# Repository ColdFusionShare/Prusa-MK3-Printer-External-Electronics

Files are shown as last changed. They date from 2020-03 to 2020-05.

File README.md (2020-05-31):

# Prusa External Electronics
A project to enable moving PSU, EINSY, and LCD out of your enclosure.

- BOM (updated with missing front and back panel parts)
- Fusion 360 source files added

Overall View:
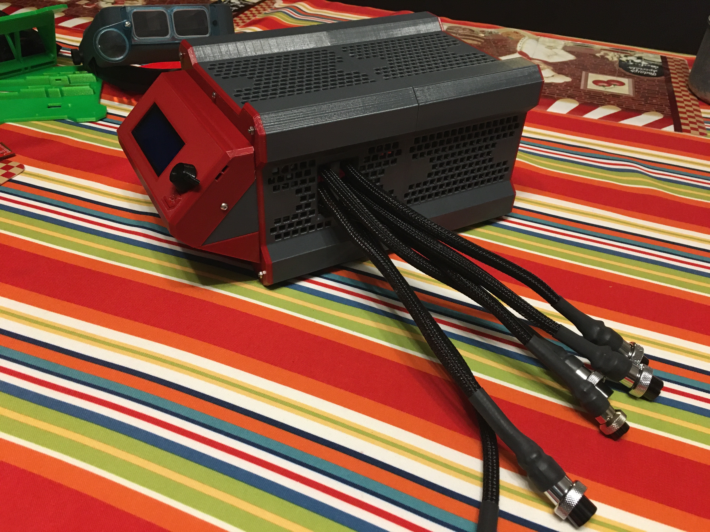
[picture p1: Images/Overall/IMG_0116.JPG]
Overall View


Cable Gland:
- Detaches easily to allow EINSY to slide back without taking cabling apart.
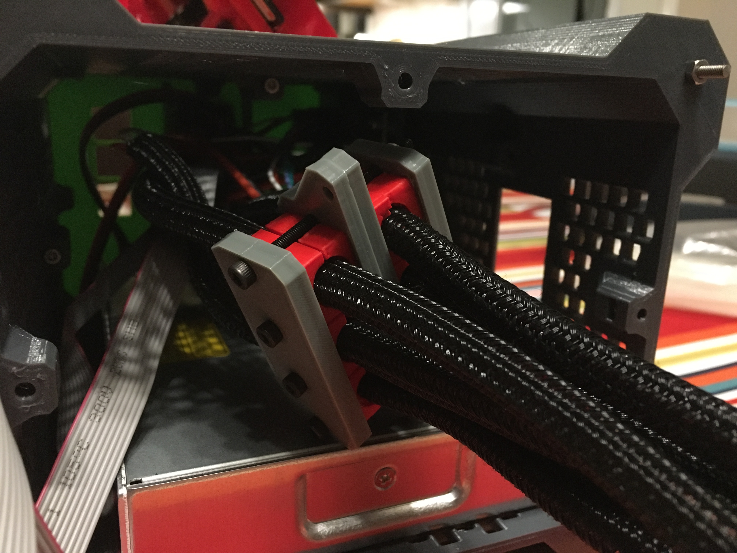
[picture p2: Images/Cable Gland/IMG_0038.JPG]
Cable Gland


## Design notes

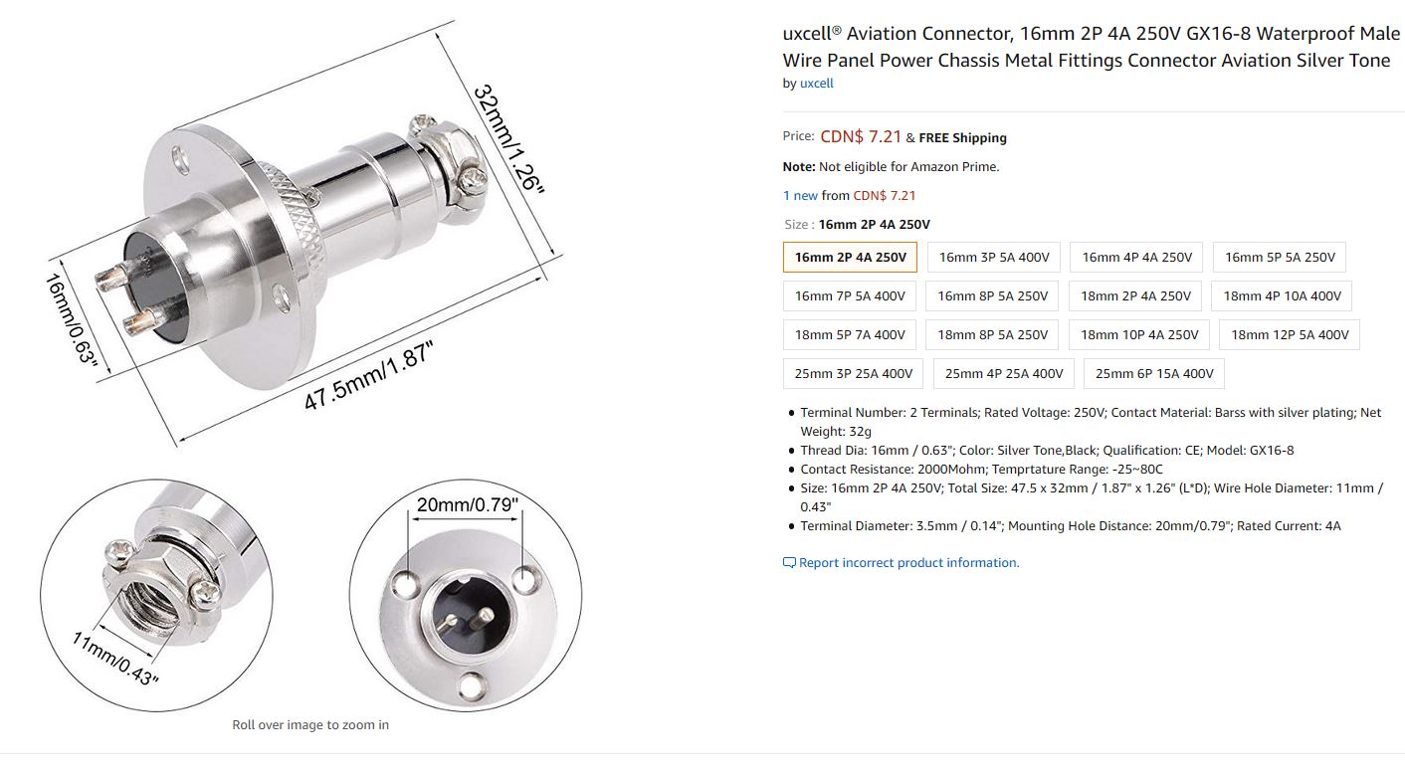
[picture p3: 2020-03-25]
Docs/gx20_16mm.JPG

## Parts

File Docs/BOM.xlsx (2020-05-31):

Item | Description | Assembly | Quantity Required | Sourced From | Part No | Lead-Time | Link | Comment
1 | 18mm 10P 4A 250V | External case cables & Lower Printer Case | 1 | Ebay |  | long | https://www.ebay.com/itm/WD19-GX20-2pin-12Pin-Aviation-Plug-Connector-19mm-20mm-Mount-Circular-Bulkhead/132708407252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
 |  |  |  |  |  |  | (link is for all circular connectors - make sure to pick the correct ones from the list and not the link above)
2 | 18mm 8P 5A 250V | External case cables & Lower Printer Case | 1 | Ebay |  | long
3 | 18mm 12P 5A 400V | External case cables & Lower Printer Case | 1 | Ebay |  | long
4 | 16mm 9P 4A 250V | External case cables & Lower Printer Case | 1 | Ebay |  | long
5 | 18mm 4P 10A 400V | External case cables & Lower Printer Case | 1 | Ebay |  | long
6 | 16mm 6P 7A 400V | External case cables & Lower Printer Case | 1 | Ebay |  | long
7 | Black socket connector - 5 pin |  | 1 | Digikey | WM2536-ND | Short |  | Single connector Y for MMU2 and PINDA2
8 | Black socket connector - 4 pin |  | 5 | Digikey | WM2535-ND | Short
9 | Black socket connector - 3 pin |  | 2 | Digikey | WM2534-ND | Short
10 | Black socket connector - 2 pin |  | 2 | Digikey | WM2533-ND | Short
11 | Contacts for Housing housings above |  | 50 | Digikey | WM2515-ND | Short
12 | Black connector - 5 pin |  | 1 | Digikey | WM8037-ND | Short |  | Single connector for MMU2 and PINDA2 connections
13 | Contacts for black connector above |  | 10 | Digikey | WM2580CT-ND | Short
14 | Black connector - 4 pin |  | 5 | Digikey | WM2902-ND | Short
15 | Black connector - 3 pin |  | 2 | Digikey | WM2901-ND | Short
16 | Black connector - pin |  | 2 | Digikey | WM2900-ND | Short
17 | Contacts for Housing housings above |  | 50 | Digikey | WM2512-ND | Short
18 | Self wrap 1/4" x 25' black |  | 1 | Digikey | 1030-FN0.25BK25-ND | Short
19 | Heat shrink 3:1 with glue 1/2" |  |  | Digikey |  | Short |  | I did not get glue and they came loose
20 | Heat shrink for circular connectors
 | depends on wire size - just get a selection |  |  | Digikey |  | Short
 | to use
21 | M3 bolts and nuts - various lengths | General
22 | M3 bolts long for cable gland (measure) | General
23 | M3 threaded rods 250 mm length | General | 4 | Amazon |  | Medium
25 | PWR ENT MOD RCPT IEC320-C14 PNL | External Case Back Cover | 1 | Digikey | Q307-ND | Short
 | 10A
26 | FUSE GLASS 5A 250VAC 5X20MM | External Case Back Cover | 2 | Digikey | F1748-ND | Short
 | (or similar 5A of this size) |  | Get spares
24 | SWITCH PUSHBUTTON SPST 5A 125V | External Case Front Cover | 1 | Digikey |  | Short
26 | 24 VDC Fan - looking for specs | External Case Front Cover | 1 | Digikey | ? | Short

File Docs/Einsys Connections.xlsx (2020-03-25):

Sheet: Pin Reference
 |  | 31 pins
 |  |  |  |  |  |  |  |  | Cable Connector | Plug In Connector
 |  |  | EINSY |  |  |  |  |  | Vendor | Vendor
Cable | Function | Name | Board Connector | Pin | Pin Detail | Wire Size | Pin Count | Vendor | Part No | Part No | Voltage | Current
Motors
 | Stepper Motor | Motor X | J8 | 1 |  | 22-24 | 4 | Digikey | WM2902-ND | WM2535-ND
 |  |  |  | 2 |  | 22-24
 |  |  |  | 3 |  | 22-24
 |  |  |  | 4 |  | 22-24
 | Stepper Motor | Motor Y | J9 | 1 |  | 22-24 | 4 | Digikey | WM2902-ND | WM2535-ND
 |  |  |  | 2 |  | 22-24
 |  |  |  | 3 |  | 22-24
 |  |  |  | 4 |  | 22-24
 | Stepper Motor | Motor Z1 | J10 | 1 |  | 22-24 | 4 | Digikey | WM2902-ND | WM2535-ND
 |  |  |  | 2 |  | 22-24
 |  |  |  | 3 |  | 22-24
 |  |  |  | 4 |  | 22-24
 | Stepper Motor | Motor Z2 | J11 | 1 | shared with Z1 | 22-24 |  | Digikey | WM2902-ND | WM2535-ND
 |  |  |  | 2 | shared with Z1 | 22-24
 |  |  |  | 3 | shared with Z1 | 22-24
 |  |  |  | 4 | shared with Z1 | 22-24
 |  |  |  |  | Total |  | 12
Extruder Cable
 | Stepper Motor | Extruder | J12 | 1 |  | 22-24 | 4 | Digikey | WM2902-ND | WM2535-ND
 |  |  |  | 2 |  | 22-24
 |  |  |  | 3 |  | 22-24
 |  |  |  | 4 |  | 22-24
 |  |  |  |  |  |  |  |  |  |  |  | All Steppers | 16
 | Fan | Hot End Fan | J5 | 1 |  | 24 | 3 | Digikey | WM2901-ND | WM2534-ND
 | 5V |  |  | 2 |  | 24
 |  |  |  | 3
 | Fan | Print Fan | J4 | 1 |  | 24 | 3 | Digikey | WM2901-ND | WM2534-ND
 | 5V |  |  | 2 |  | 24
 |  |  |  | 3 |  | 24
 | Extruder | Thermistor | J2 | 1 | GND | 24 | 2 | Digikey | WM2900-ND | WM2533-ND
 |  |  |  | 2 |  | 24
 | Extuder Heater | Heater | X13 | 1 |  | 20? | 2 | Digikey | 277-1011-ND | 277-1150-ND
 |  |  |  | 2 |  | 20?
 | Pinda Sensor | Pinda Probe | J15 | 1 |  | 24 | 4 | Digikey | WM2902-ND | WM2535-ND
 |  |  |  | 2 |  | 24
 |  |  |  | 3 | GND | 24
 |  |  |  | 4 | VCC | 24
 | Filament Sensor | Filament Sensor | P3 (lower row) | 2 | VCC | 24 | 5 | Digikey | WM8037-ND | WM2536-ND
 |  |  | pins 2,4,6,8,10 | 4 | GND | 24
 |  |  |  | 6 |  | 24
 |  |  |  | 8 |  | 24
 |  |  |  | 10 |  | 24
 |  |  |  |  | Total |  | 23 |  |  |  |  | All Signal | 19
MMU
 | MMU connection |  | P3 (upper row) | 1 | VCC | 24 | 5 | Digikey | WM8037-ND | WM8249-ND
 |  |  | pins 1,3,5,7,9 | 3 |  | 24
 |  |  |  | 5 |  | 24
 |  |  |  | 7 | GND | 24
 |  |  |  | 9 |  | 24
 |  |  |  |  | Total |  | 5
Heat Bed
 | Heat Bed | Heat | Screw Terminal | 1 |  | 14 | 2
 |  |  |  | 2 |  | 14
 | Heat Bed | Thermistor | J6 | 1 | GND | 24 | 2 | Digikey | WM2900-ND | WM2533-ND
 |  |  |  | 2 |  | 24
 |  |  |  |  | Total |  | 4 |  |  |  |  | All Heater Lines | 4
 |  |  |  |  | Grand Total |  | 44
 |  |  |  |  |  |  |  |  |  |  |  | Total | 39
 | Power Failure | Power Panic |  | 1 |  |  | 2 | Digikey | WM2900-ND
 |  |  |  | 2
 | Bed Power Input | PSU Power IN |  | 1 |  |  | 2
 |  |  |  | 2
 | Power Input | PSU Power IN |  | 1 |  |  | 2
 |  |  |  | 2
 | https://github.com/PrusaOwners/prusaowners/wiki/MK3_Compatible_Parts
 | erminal / Pin for keyed connectors | Female terminals (pins) used in 4-pin and 3-pin keyed connectors on the Einsy board. |  | Molex: 16-02-0097 | Mouser: 538-16-02-0097 (https://www.mouser.com/ProductDetail/Molex/16-02-0097?qs=sGAEpiMZZMtVoztFdqDXO%252bpSlI4T0Hse)
 |  |  |  |  | DigiKey: WM2513-ND (https://www.digikey.com/products/en?keywords=16-02-0097)
 |  |  |  |  | TME: MX-16-02-0097 (https://www.tme.eu/en/details/mx-16-02-0097/raster-signal-connectors-254mm/molex/016020097-70058-0206/)

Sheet: Wiring Guide
 | External Case | EINSY |  |  |  |  |  |  |  | Printer Side
 | Circular Connector Type | Connector | Prusa | My |  |  | Board | Board |  | In-line connector
Signal Type | (for cables going outof case) | Pin Number | Color | Color | Function | Name | Connector | Pin |  | (from bulk head circular Connectors) | AWG | Comment
Motor
 | 18mm 10P 4A 250V
 |  | 1 | Black | Black | Stepper Motor | Motor X | J8 | 1 |  | WM2535-ND | 22
 |  | 2 | Green | Green |  |  |  | 2
 |  | 3 | Red | Red |  |  |  | 3
 |  | 4 | Blue | Blue |  |  |  | 4
 |  | 5 | Black | Black | Stepper Motor | Motor Y | J9 | 1 |  | WM2535-ND | 22
 |  | 6 | Green | Green |  |  |  | 2
 |  | 7 | Red | Red |  |  |  | 3
 |  | 8 | Blue | Blue |  |  |  | 4
 |  | 9 |  |  | Unused
 |  | 10 |  |  | Unused
 | 18mm 8P 5A 250V | 1 | Black | Black | Stepper Motor | Motor Z1/Z2 | J10/J11 | 1 |  | WM2535-ND | 22 | Split into two connectors for Z. For SKR 1.4 used 4 unused lines on 9 Pin circular connector
 |  | 2 | Green | Green |  |  |  | 2
 |  | 3 | Red | Red |  |  |  | 3
 |  | 4 | Blue | Blue |  |  |  | 4
 |  | 5 | Black | Black | Stepper Motor | Extruder | J12 | 1 |  | WM2535-ND | 22
 |  | 6 | Green | Green |  |  |  | 2
 |  | 7 | Red | Red |  |  |  | 3
 |  | 8 | Blue | Blue |  |  |  | 4
Signal
 | 18mm 12P 5A 400V
 |  | 1 | black | black | Fan | Hot End Fan | J5 | 1 |  | WM2534-ND | 22
 |  | 2 | red | red | 5V |  |  | 2
 |  | 3 | yellow | green | tach |  |  | 3
 |  | 4 | black | black | Fan | Print Fan | J4 | 1 |  | WM2534-ND | 22
 |  | 5 | red | red | 5V |  |  | 2
 |  | 6 | yellow | green | tach |  |  | 3
 |  | 7 |  | black | Extruder | Thermistor | J2 | 1 |  | WM2533-ND | 22
 |  | 8 |  | red |  |  |  | 2
 |  | 9 | white | white | Pinda Sensor | Pinda Probe | J15 | 1 |  | WM2535-ND
 |  | 10 | black | black |  |  |  | 2
 |  | 11 | blue | red |  |  |  | 3
 |  | 12 | brown | green |  |  |  | 4
 | 16mm 9P 4A 250V
 |  | 1 | white | white | Filament Sensor MK3S | Filament Sensor | P3 (lower row) | 2 |  | WM2536-ND
 |  |  |  |  |  |  | pins 2,4,6,8,10 | 4 | NC
 |  |  |  |  |  |  |  | 6 | NC
 |  | 2 | black | black |  |  |  | 8
 |  | 3 | red | red |  |  |  | 10
 |  | 4 |  | black | Heat Bed | Thermistor | J6 | 1 |  | WM2533-ND | 22
 |  | 5 |  | red |  |  |  | 2
 |  | 6 |  |  | Unused
 |  | 7 |  |  | Unused
 |  | 8 |  |  | Unused
 |  | 9 |  |  | Unused
Heat
 | 18mm 4P 10A 400V
 |  | 1 |  | Red | Extuder Heater | Heater | X13 | 1 |  | 16 AWG | 16 | Wago?
 |  | 2 |  | Black |  |  |  | 2
 |  | 3 |  | Red | Heat Bed | Heat | Screw Terminal | 1 |  | 14 AWG | 14 | Red screw terminals
 |  | 4 |  | Black |  |  |  | 2
MMU
 | 16mm 6P 7A 400V
 |  | 1 | brown | red | MMU connection |  | P3 (upper row) | 1 |  | WM2536-ND
 |  |  |  |  |  |  | pins 1,3,5,7,9 | 3 | NC
 |  | 2 | green | green |  |  |  | 5
 |  | 3 | white | white |  |  |  | 7
 |  | 4 | blue | blue |  |  |  | 9
 |  | 5 | red | red |  |  |  |  |  | mmu +24V | 16 | 16 AWG
 |  | 6 | black | black |  |  |  |  |  | mmu ground |  | 16 AWG

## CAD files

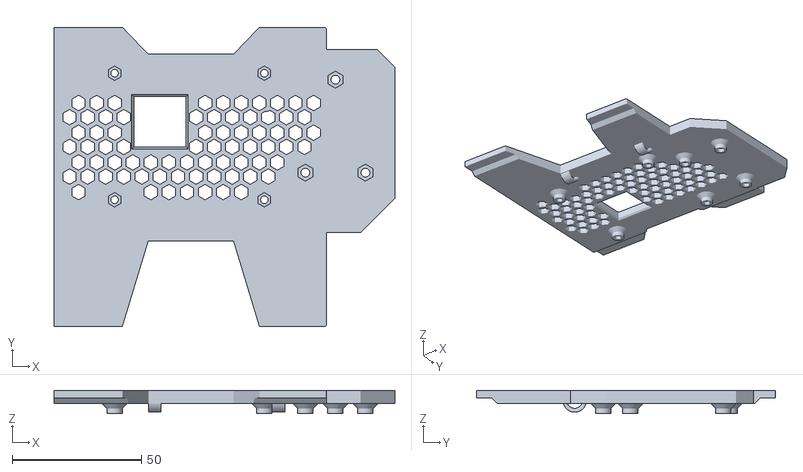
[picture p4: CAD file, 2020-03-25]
Printed Parts/Boards/PCB Holder (Rpi3).stl
132.0 x 115.7 x 9.00

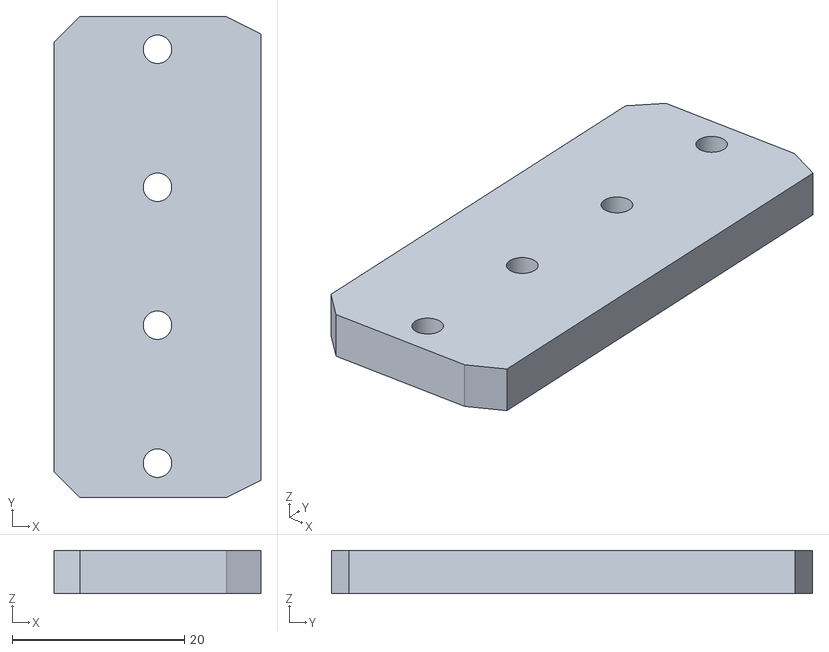
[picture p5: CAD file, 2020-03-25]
Printed Parts/Cable Gland/CGF Top.stl
24.0 x 55.8 x 5.00

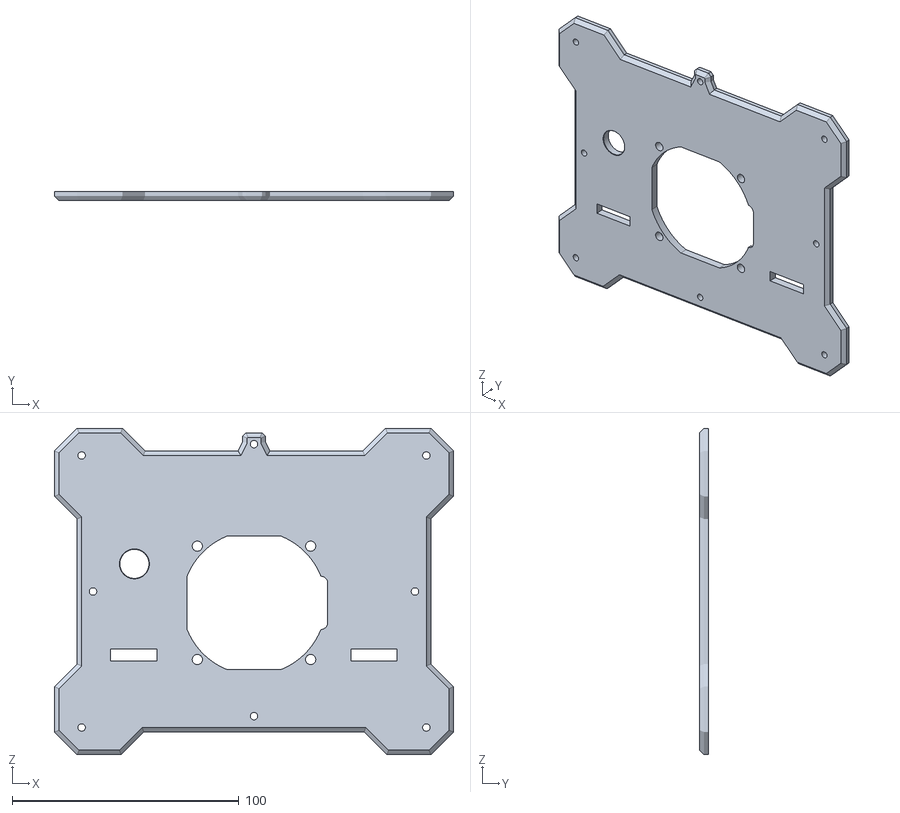
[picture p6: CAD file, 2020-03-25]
Printed Parts/Frame/FrameSlice_Front_Cover.stl
176.0 x 4.00 x 144.0

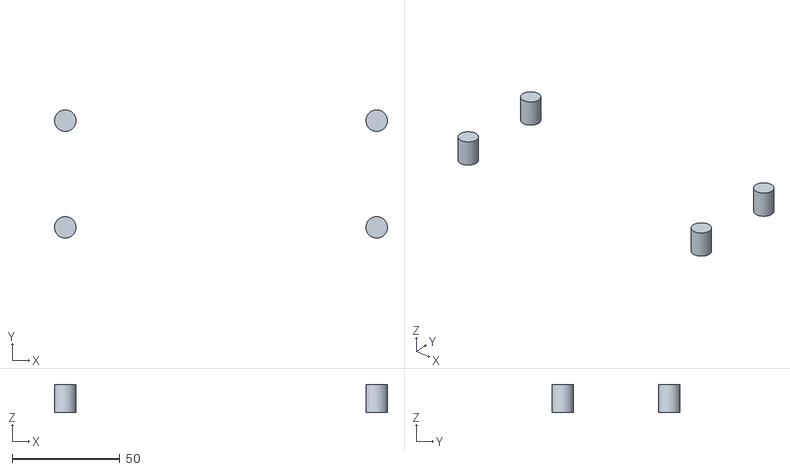
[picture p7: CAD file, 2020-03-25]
Printed Parts/LCD/LCD Custom Support Blockers.stl
154.5 x 59.5 x 13.1

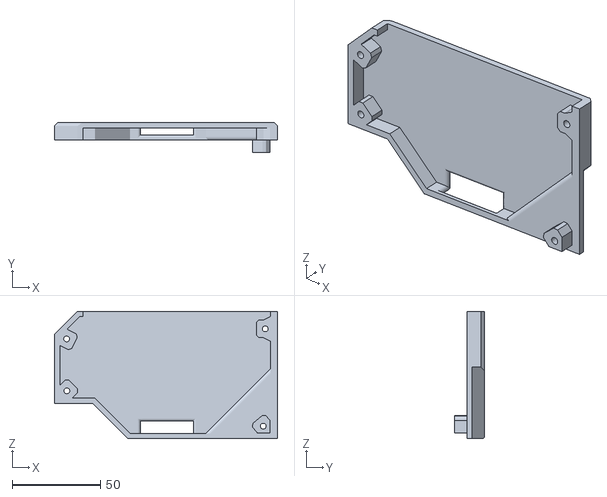
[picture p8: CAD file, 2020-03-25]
Printed Parts/Printer/Lower Case Cover v2.stl
126.0 x 17.0 x 72.0

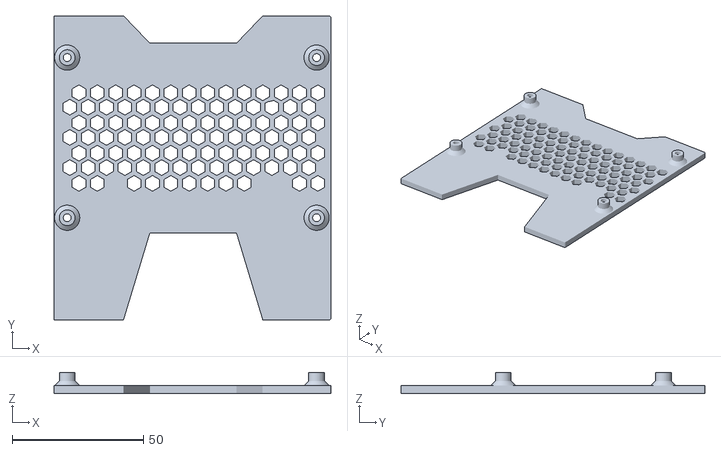
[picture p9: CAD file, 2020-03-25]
Printed Parts/Boards/PCB Holder (Einsy).stl
105.5 x 115.7 x 8.00

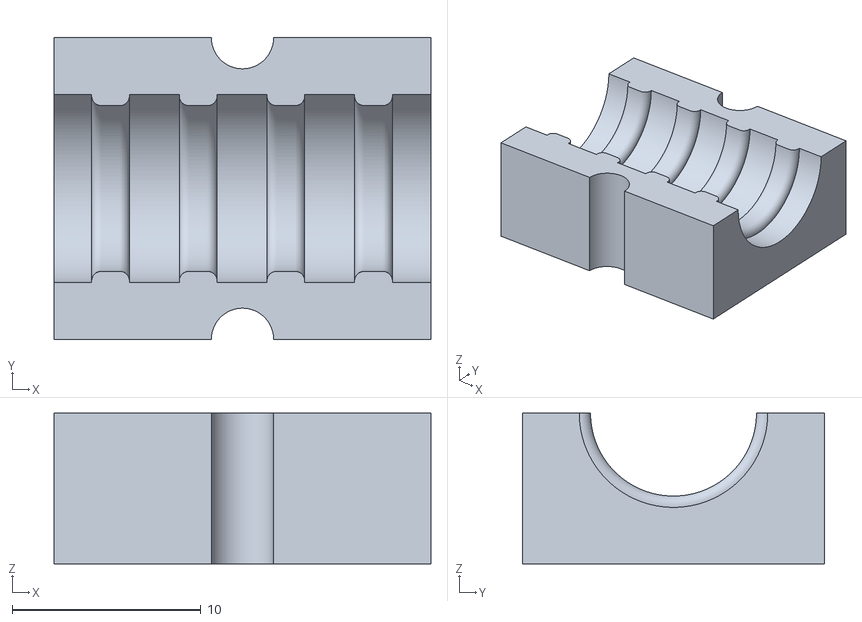
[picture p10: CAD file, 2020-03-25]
Printed Parts/Cable Gland/Cable_Gland_Bottom_Or_Top.stl
20.0 x 16.0 x 8.00

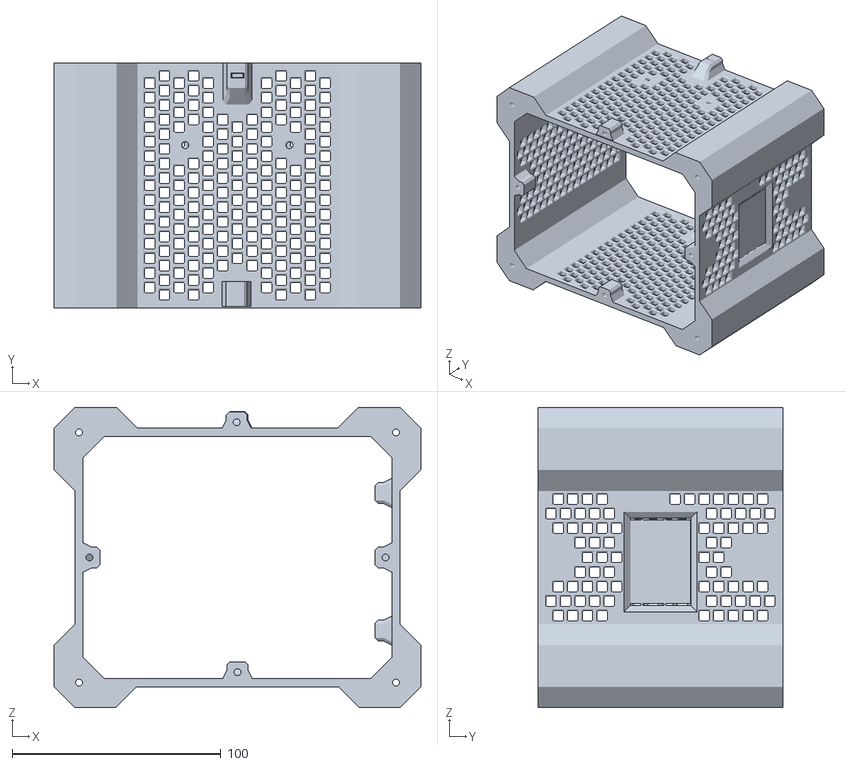
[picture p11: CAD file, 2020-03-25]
Printed Parts/Frame/FrameSlice_Front_v2.stl
176.0 x 117.5 x 144.0

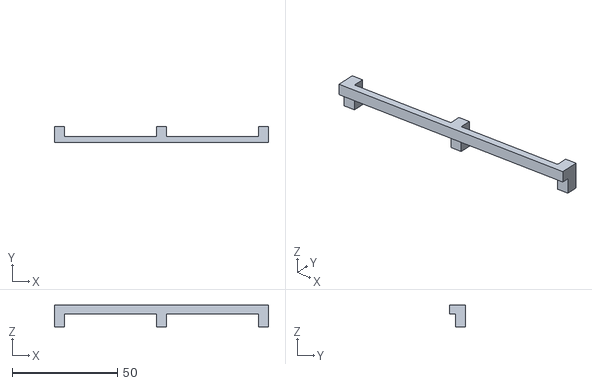
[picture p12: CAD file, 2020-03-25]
Printed Parts/LCD/LCD Lower Inside Support.stl
101.9 x 7.72 x 10.3

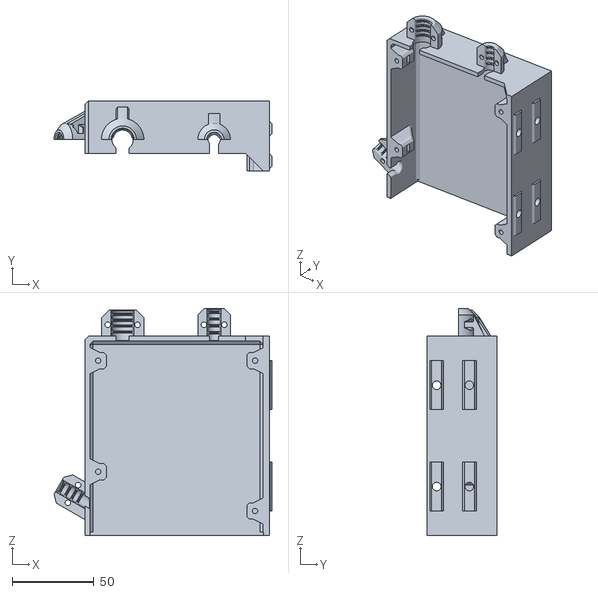
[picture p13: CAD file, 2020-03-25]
Printed Parts/Printer/Upper Case.stl
133.4 x 42.8 x 139.0

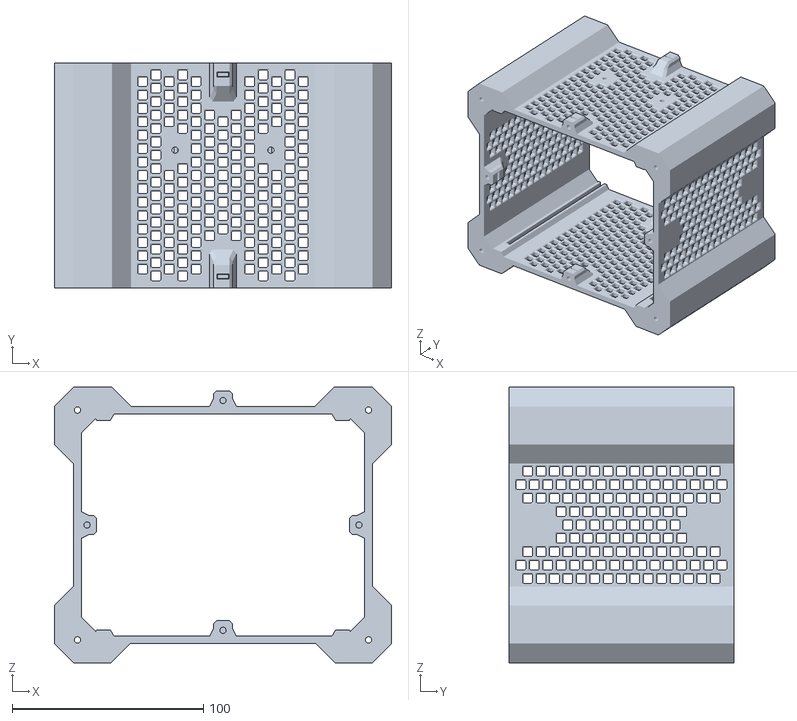
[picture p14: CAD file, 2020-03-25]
Printed Parts/Frame/FrameSlice_Back_v2.stl
176.0 x 117.5 x 144.0

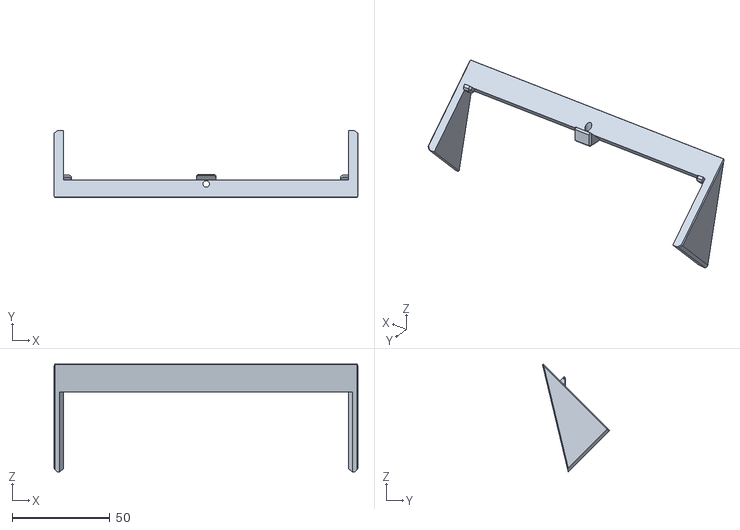
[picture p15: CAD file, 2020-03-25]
Printed Parts/LCD/LCD Bottom Enclosure.stl
155.8 x 34.4 x 55.3

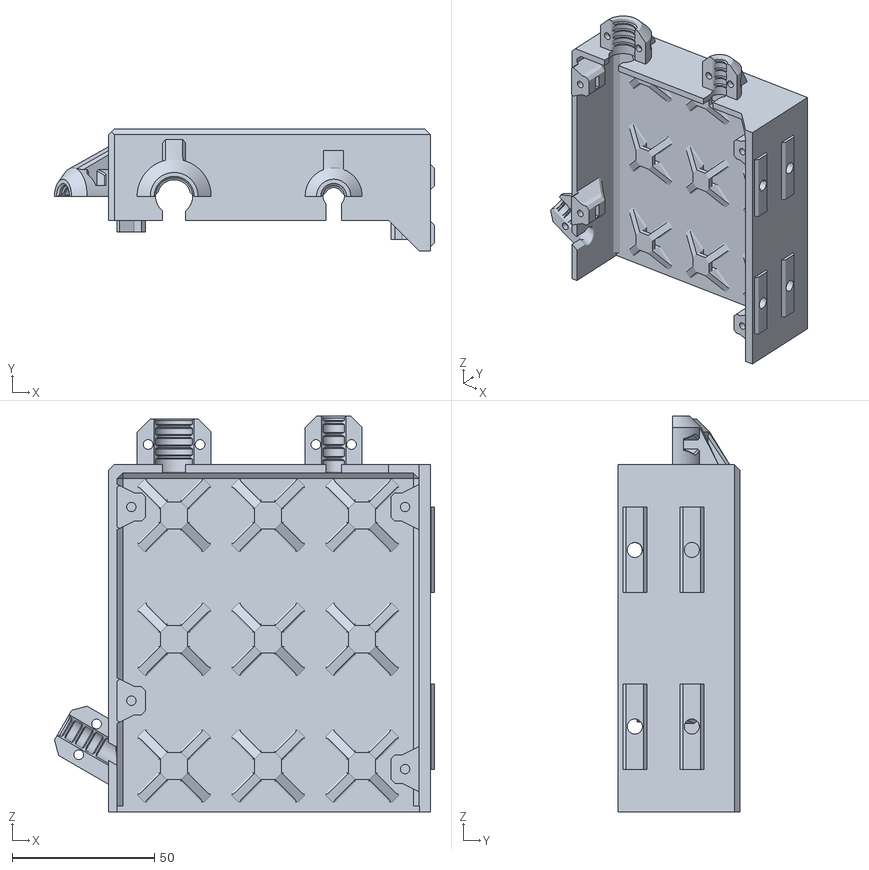
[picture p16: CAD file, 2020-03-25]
Printed Parts/Printer/Upper Case v2.stl
133.4 x 42.8 x 139.0

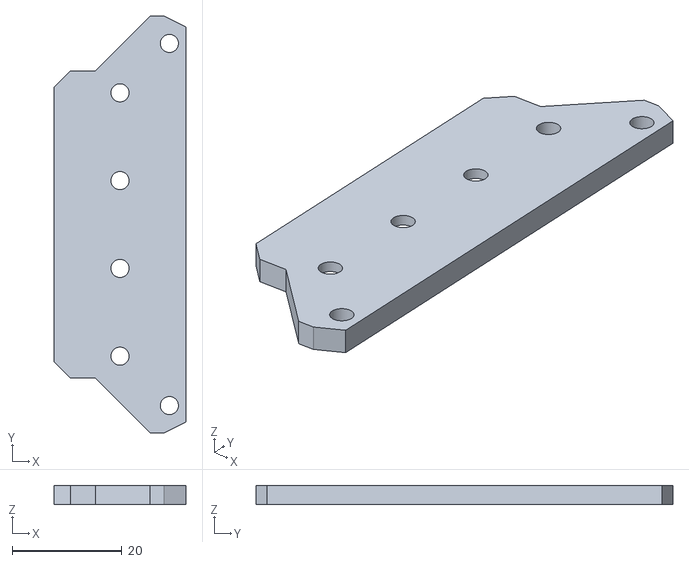
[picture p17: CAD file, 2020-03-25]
Printed Parts/Cable Gland/CGF Middle - Bottom.stl
24.0 x 76.0 x 3.50

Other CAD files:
Printed Parts/Cable Gland/CGF Bottom.stl
Printed Parts/Frame/FrameSlice_Back_Cover.stl
Printed Parts/LCD/LCD Cover.stl
Printed Parts/Printer/Cable Heat Bed Clamp Top.stl
Printed Parts/Cable Gland/CGF Middle - Top.stl
Printed Parts/Cable Gland/Cable Gland Frame Bolt v62.f3z
Printed Parts/LCD/LCD Custom.stl
Printed Parts/Printer/Cable Extruder Clamp Top.stl
Printed Parts/Printer/Cable X Motor Clamp Top.stl
Printed Parts/Printer/Lower Case v2.stl
Printed Parts/Printer/Lower Case.stl
Printed Parts/Printer/Upper Cover v2.stl
Printed Parts/Printer/Upper Cover.stl

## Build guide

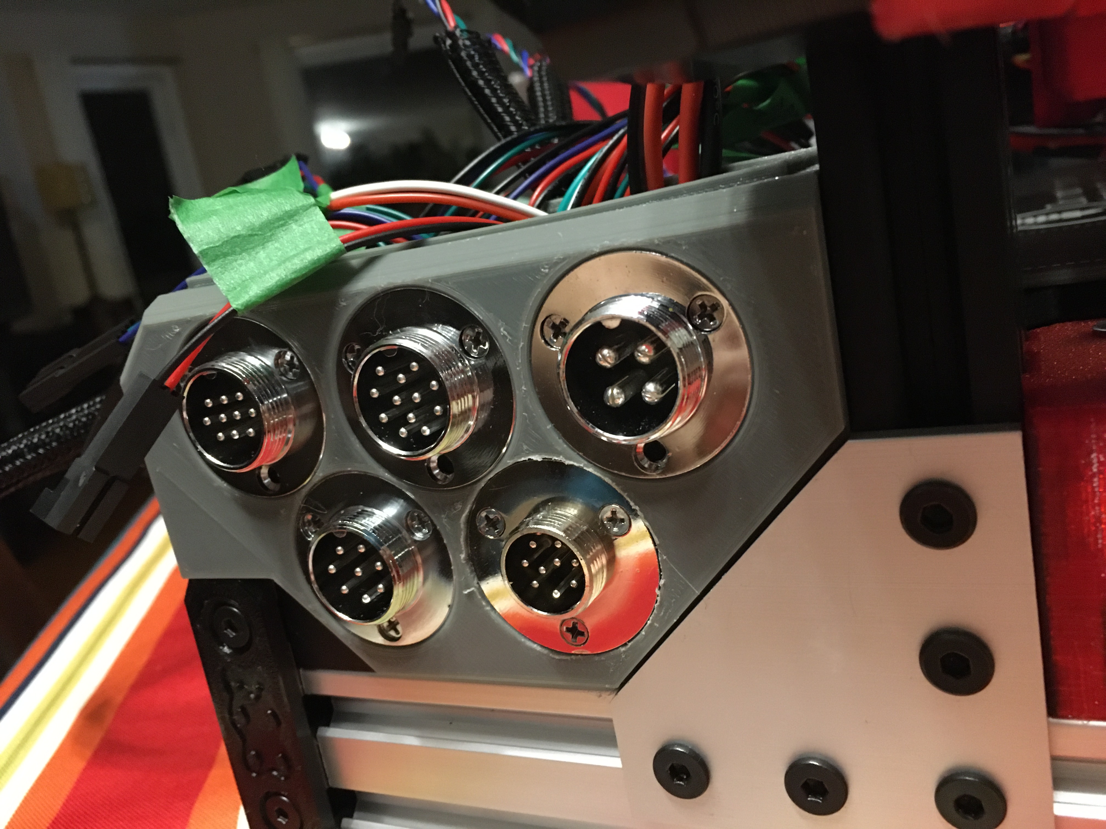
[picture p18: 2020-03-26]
Images/Printer Connections and Case/IMG_0027.JPG

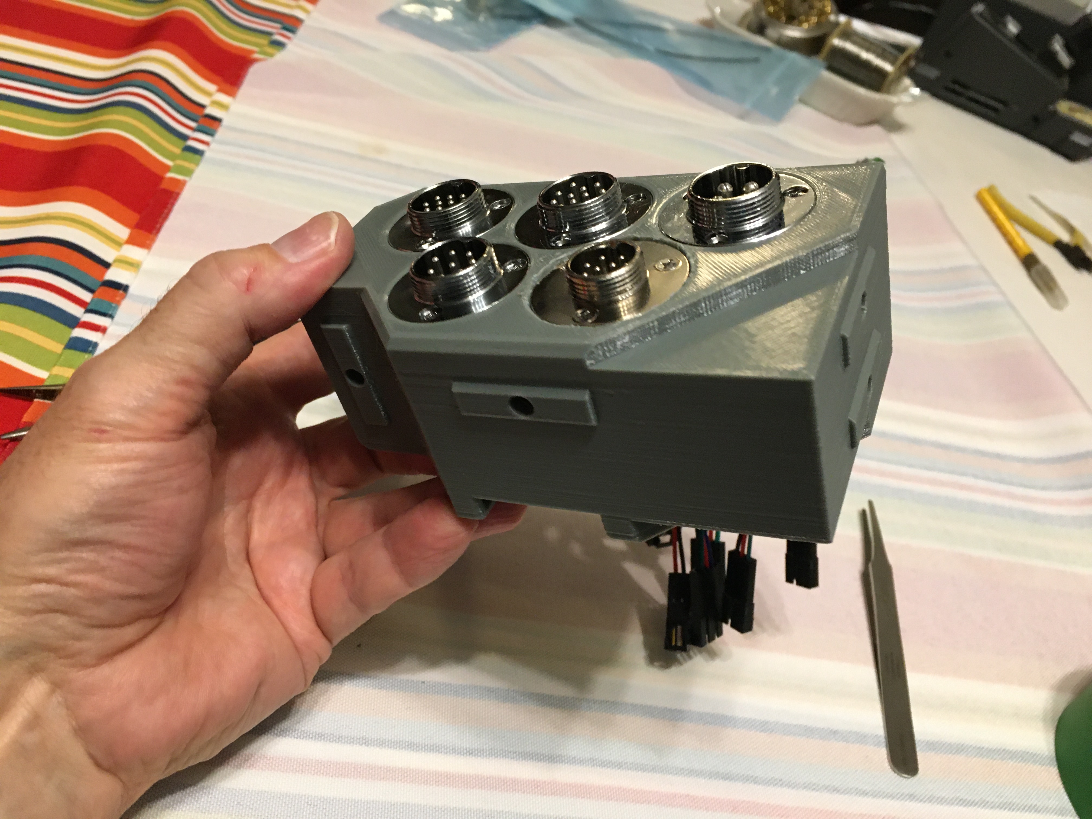
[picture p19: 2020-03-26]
Images/Printer Connections and Case/IMG_0024.JPG

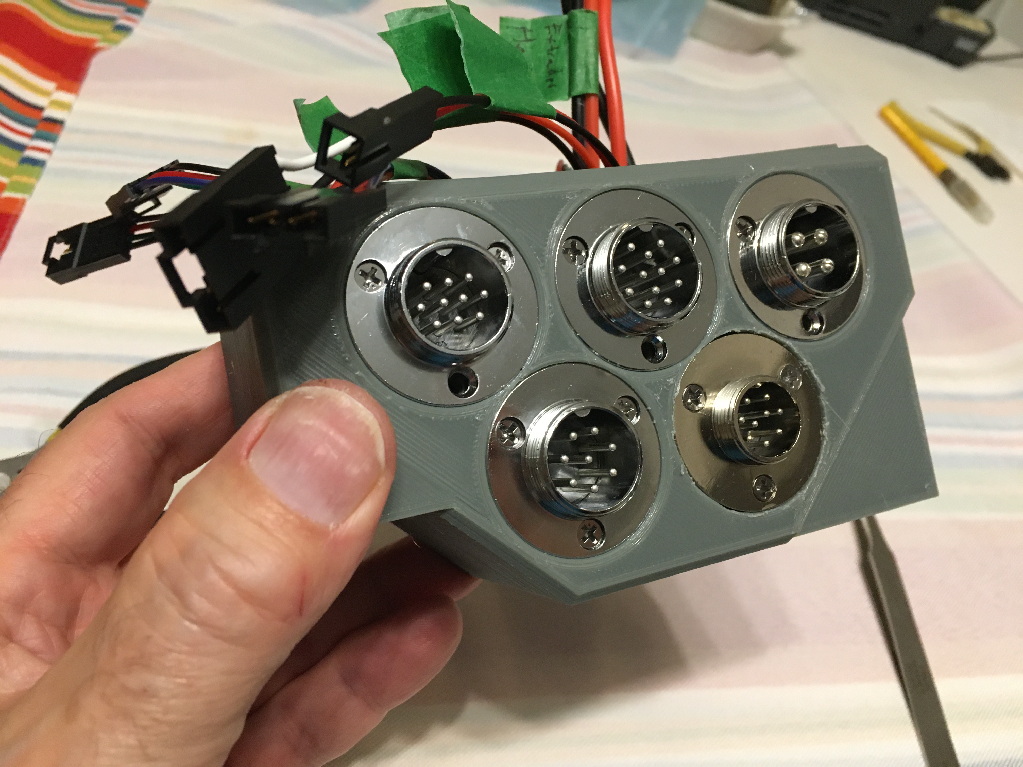
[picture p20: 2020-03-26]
Images/Printer Connections and Case/IMG_0022.JPG

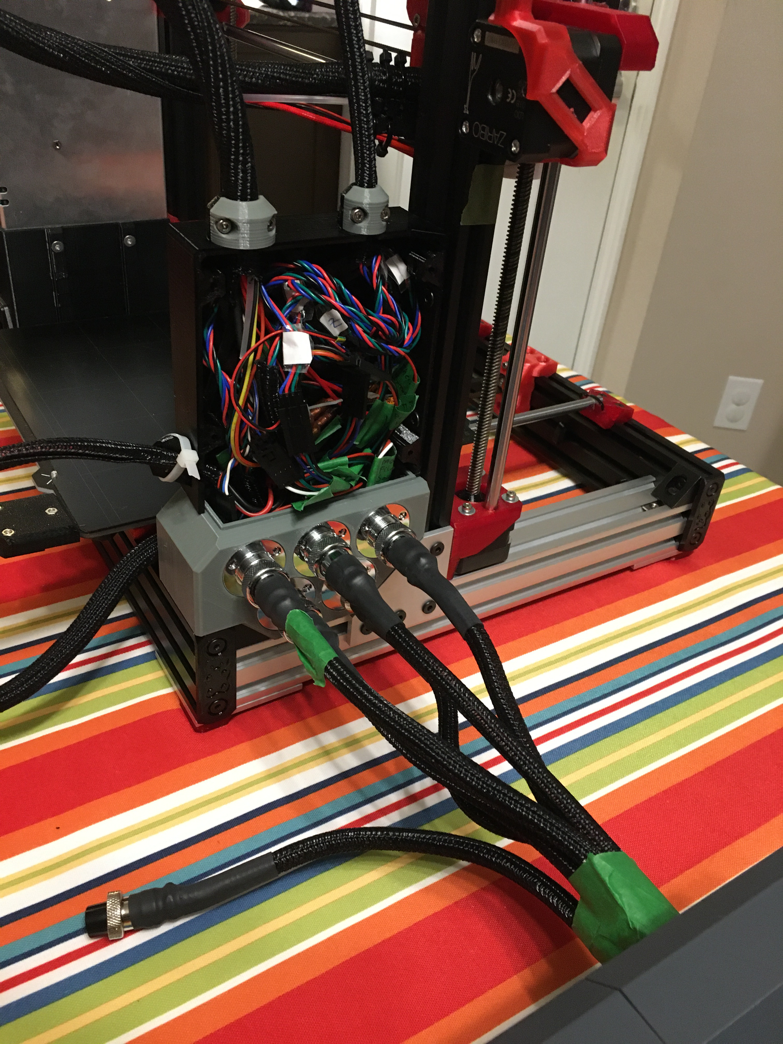
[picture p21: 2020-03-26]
Images/Printer Connections and Case/IMG_0032.JPG

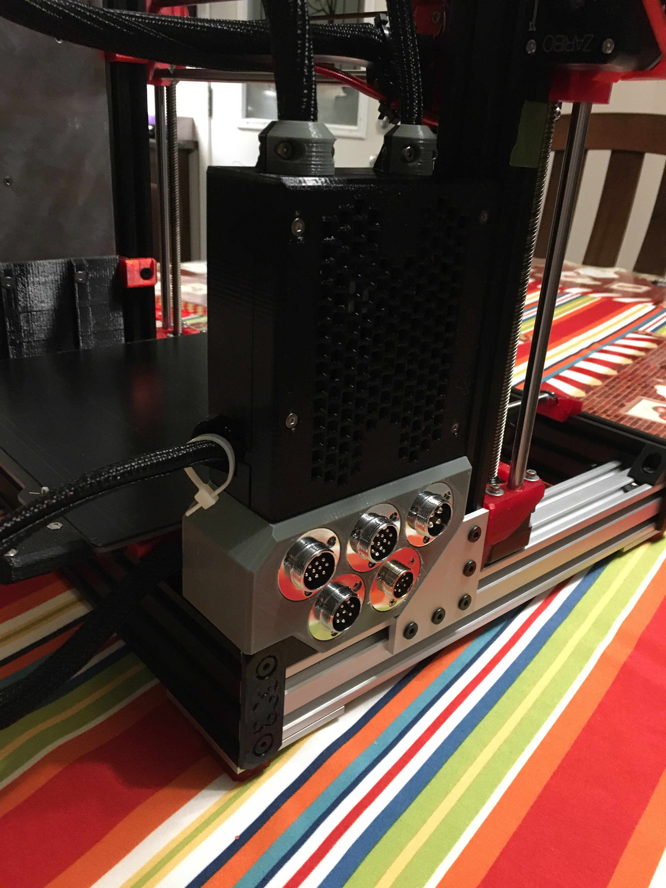
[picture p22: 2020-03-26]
Images/Printer Connections and Case/IMG_0036.JPG
